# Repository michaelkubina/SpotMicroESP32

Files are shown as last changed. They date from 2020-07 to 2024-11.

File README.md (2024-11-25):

# SpotMicroESP32

My take on a SpotMicro with an optimized design for supportfree 3D-printing and integration of an ESP32-DevKitC. This is still a Work-in-Progress!

You can find the 3D-printing parts on Thingiverse as well: https://www.thingiverse.com/thing:4559827/files

- Join the Discord-Channel for this remix: https://discord.gg/s8F6xHGk9Y (#spotmicro-esp32)
- ~Join the Slack-Channel for this remix - discuss any topics regarding this design: spotmicroai.slack.com (#spotmicro-esp32)~ Due to no active subscription there is no possibility to browse through older posts. This is why a lot of people moved to the discord channel.

This Project currently lacks the whole programming/software part. Luckily Maarten Weyn already made the inverse kinematics work and wrote also an Smartphone App for simple Control of this Robot via BLE. There is no walking gait implementation though. I still advice to take a look into his Repository as well, as this currently my preferred codebase:
https://github.com/maartenweyn/SpotMicro_ESP32

The Discord user Blacksheep created a impressive fork of this project, that utilizes a custom designed PCB for component placement and a FSI6 remote control in order to operate the robot. The codebase implements the inverse kinematics and even walking gait for it. Since its packed as an arduino project, its simpler to get started with it then with the ESP-IDF. You can find the repo here:
https://github.com/Blacksheep909/SpotMicroESP32-Nitro-Fork/tree/master

The SpotMicro-Leika project sources different SpotMicro projects and combines them into a feature-rich build. It offers an FreeRTOS implementation, is under active development and has the inverse kinematics and two gaits implemented. You should definetly check it out:
https://github.com/runeharlyk/SpotMicroESP32-Leika

Also there's a walking gait implementation and voice-commanding by Guna R. from the slacks #spotmicro-esp32 channel, whis is build upon Maartens software (see Repo above). You definitly have to take a look there as well - but it seems the repos sourcecode is incomplete and missing the app:
https://github.com/cholan2100/ceasar

Look also at the GitLab pages for the general SpomicroAI community, where you can find different models and resources: https://gitlab.com/custom_robots/spotmicroai

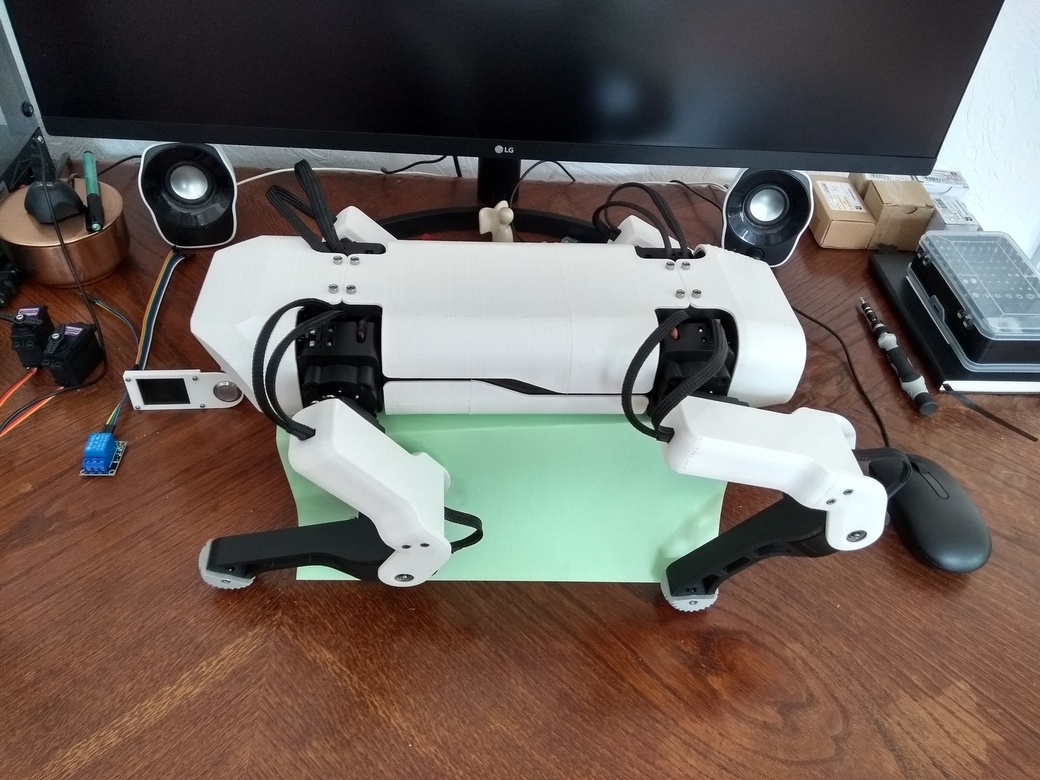
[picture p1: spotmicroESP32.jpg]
SpotMicroESP32


## Note of thanks
I want to thank Deok-yeon Kim (KDY0523) for his beautyful and well thought out design of the SpotMicro, without whom my derivate would not have been possible. You can find his original Design here on Thingiverse: https://www.thingiverse.com/thing:3445283

Him sharing the files with an open licence, made it possible to let it grow a community around it. This is why i want to reference to them as well - the SpotMicroAI Community: https://spotmicroai.readthedocs.io/en/latest/

## Preface
This is a work-in-progress, with rather loose milestones.

For 2020 there are two goals:
- ~to redesign the original parts, so that they could be printed without any support~ (done)
- ~to make a circuitry for all sensors and parts, that possibly would fit and be considered necessary~ (done)

~For 2021 there are two main goals and one optional goal:
- to write my own firmware with the [ESP-IDF](https://github.com/michaelkubina/SpotMicroESP32/tree/master/code#esp-idf), that integrates/utilizes all sensors and modules except the ESP-CAM which needs its own firmware (in progress)
- to write a smartphone App in Flutter, that connects to the firmware and reads from/writes to the robot (in progress)
- to implement the inverse kinematics (optional goal)~

This repository is currently just my hobby and as such, it will have its own pace. This being said, i am still happy about any questions, collaborations, suggestions, ideas, forks and what else comes to your mind. I want you to participate, because i think there are a lot of things, that you could dig into.

## Sections

* [3D-printed Partlist](https://github.com/michaelkubina/SpotMicroESP32/blob/master/parts/SpotMicroESP32_parts_v1_0_0/)
* [Bill of Materials](https://github.com/michaelkubina/SpotMicroESP32/#bill-of-material)
* [Assembly Guide](https://github.com/michaelkubina/SpotMicroESP32/blob/master/assembly/)
* [Electronics](https://github.com/michaelkubina/SpotMicroESP32/blob/master/electronics/)
* [Programming](https://github.com/michaelkubina/SpotMicroESP32/blob/master/code/)
* [Inverse Kinematics](https://github.com/michaelkubina/SpotMicroESP32/blob/master/kinematics/)

## Bill of Material
The following Section will describe in detail the different parts needed for your own SpotMicroESP32 build, with at least some rough estimate of the price.

### 3D-Printing
To build your own SpotMicroESP32 you will need to print a lot parts. For an overview of the 3D printed parts needed, please visit the [3D-printed Partlist](https://github.com/michaelkubina/SpotMicroESP32/blob/master/parts/SpotMicroESP32_parts_v1_0_0/). It might be necessary to remix some of the templates to suit your needs, when chosing other electronic components than those listet here.

### Electronics
The SpotMicroESP32 ist still a Work-in-Progress and as such the BOM might change as well - check the "deprecated" section for changes. There are still some parts missing and some others are not tested yet - those status will be marked as such. I will give a rough price estimate, which may or may not work for you and might be out of date at some point.

| part or module | number | short description | status | estimated price | 
|---|---|---|---|:---|
| ESP32-DevKitC 							|  1x | the core MCU for the build with WIFI + BLE capabilities. 											| tested			| 7€		|
| ESP32-CAM									|  1x | Tested with the ESP32-Module with OV2640 Camera (version 2). There are also cameras with a version 1 OV2640, where the sensor is in landscape orientation and not in portrait. Also the flexcable seems to be some millimeters shorter than the one from Version 2. You can distinguish them by the imprint on the flexcable, stating TY-OV2640-V2.0. Both OV2640 Cameras should work in theory, as the part is designed to fit both models. Definetly dont go with the one with an fisheye-lens or other variations - the field of view would be hindered and most likely the lens would not fit through the hole anyway. 																		| tested	| 10€		|
| FT232RL USB-TTL-Adapter					|  1x | USB-to-Serial Adapter for ESP32-CAM flashing														| tested			| 2€		|
| (MG996R Servo)								| 12x | The bare minimum... but with flaws like jittering and much play... 10Kg servos with metal gears and ball bearings. With these the robot is capable to stand up/change his pose but they are most likely too weak for smooth and reliable walking. **(Update 2020-11-19: It can be affirmed, that walking is possible not great, but also not horrible)** Go with these only if you can accept these limitations and if more expensive servos would mean not to try this project in the first place.  										| tested			| 5€ each 	|
| better go with DS3218MG Servo 			| up to 12x | 20Kg servos with metal gears and ball bearings. Much less play and in my tests no jittering, but also very strong. With these your robot should be able to walk **significantly better**. Maybe only 4 of these are enough, when used in the lower legs - the most stressed parts. Maybe you would need also 4 additional ones for the upper legs - but maybe MG996R are enough here. The shoulders should be comfortable with MG996R, as these dont do much heavy work.  														| partially tested	| 15€-20€ each 	|
| FSH6S Servohorn 							| 12x | servohorn used for this build (should be already shipped with your servos) otherwie use model from 3D parts 							| tested 			| n.n. 		|
| Rubber Dampeners for your Servos			| 48x | servo rubber dampeners, so you could use M3 screws (should be already shipped with your servos) 	| tested 			| n.n. 		|
| Servocable Extension						|  4x | extending the servocables of the lower legs about 10cm to 15cm 										| tested			| 10€		|
| 625ZZ Ball Bearing 						|  8x | miniature ball bearing without a flange 															| tested 			| 1€ each 	|
| WS2812b 12 LED Ring (50mm outer diameter) |  1x | Neopixel-Clone-Ring with an outer diameter of 50mm used to signal status/mood						| tested | 6€ |
| 0.96" OLED I2C Display					|  1x | small OLED screen with SSD1306 IC for status informations											| tested			| 4€		|
| HC-SR04 Ultrasonic Sensor					|  2x | ultrasonic sensor module for distance measuring														| tested			| 3€ each	|
| GY-521 Gyroscope and Accelerometer		|  1x | a module to measure accelaration and spatial orientation, which can be extented with magnetometers  | tested			| 3€		|
| PCA9685 16Channel 12Bit PWM Board			|  1x | PWM driver board used for your servos and LEDs, which can power your parts from an external source	| tested			| 5€		|
| HW-482 / KY-019 5V 10A Relais				|  1x | relais module to cut the power to your servos completely											| tested			| 3€		|
| 19mm Push Button with LED					|  1x | illuminated latching pushbutton 																	| tested			| 10€		|
| Micro-USB to DIP Adapter					|  2x | USB-Ports used for extending the USB-Ports of the ESP32 DevKitC and ESP32-CAM (TTL-Adapter)			| tested			| 2€		|
| XL4016 DC-DC 9A Stepdown Converter  		|  1x | big step-down converter to lower your LiPo 2S voltage to 6,5V **(minimum for MG996R)** | tested		 | 8€		|
| or SZBK07 DC-DC 20A Stepdown Converter  	|  1x | even bigger step-down converter to lower your LiPo 2S voltage to 6,5V **(minimum for DS3218)**	| tested		 | 12€		|
| LM2596 DC-DC or similar Stepdown Module	|  1x | small step-down converter to lower your LiPo 2S voltage 5V for ESP32's VIN and Modules 				| tested			| 2€ each	|
| ACS712 30A current sensor module			|  1x | current sensor module capable of max. 30A for e.g. emergency shutdown				 				| tested			| 2€ 		|
| 25V voltage sensor module					|  1x | simple voltage divider module for up to 25V used as a voltage sensor to determin battery charge		| tested			| 2€ 		|
| 5200mAh - 6200mAh LiPo 30C+ 2S Tamiya/XH	|  1x | beefy LiPo as your main power source ***(this is actually your individual choice)***				| tested		 	| 40€		|

#### Depecrated

The Camera-Unit in the head will be replaced by an ESP32-CAM, because its reasonably cheap (~10€) and opens up a lot of new possibilities like object-recognition, because of additional processing-power.

| part or module | number | short description | status | estimated price | 
|---|---|---|---|:---|
| OV7670 VGA-Camera Module w/o FIFO			|  1x | VGA-Camera without framebuffer IC, used with lower resolution due to memory restrictions **(replaced by ESP32-CAM)**			| tested			| 3€		|
| 5mm ~3V LEDs (White)						|  6x | LEDs used as your camera-lights	**(replaced by ESP32-CAM internal flashlight)**													| tested			| 1€		|
| 5mm ~3V RGB-LEDs							|  2x | RGB-LEDs used as an underglow, might signal status or mood **(replaced by Neopixel-Generica)**									| tested			| 1€		|
| 1,77" TFT with ST7735 w/o SD				|  1x | small TFT screen with ST7735 IC for status informations **(replaced by 1.8" TFT with SD-Card)**									| tested			| 7€		|
| optional WS2812B Pixelboard				|  4x | Neopixel-Clones (SMD LED's on small round PCB) used as an underglow, might signal status or mood	**(removed, as the result is underwealming** | tested			| 1€		|
| 1,8" TFT with ST7735 with SD				|  1x | small TFT screen with ST7735 IC for status informations	**(replaced by 0.96" OLED I2C Display)**	 |tested			| 7€		|

### Miscellaneous

| part or module | number | short description | status | estimated price | 
|---|---|---|---|:---|
| M2x8 cylinderhead screws + M2 nuts		| 84x each | screws + nuts to mount your servohorns ***(you could glue the servohorns in place instead and save yourself 72x M2x8 screws and nuts, but i have not tested it)***, also used to mount the 1,77" TFT and the pins for the ball bearings 	| tested | 8€  |
| M3x8 cylinderhead screws + M3 nuts		| 80x each | screws + nuts for the whole assembly ***(i hope i have not forgotten some, better buy in bulk as these are usefull for other projects as well)***																							| tested | 8€  |
| M3x20 cylinderhead screws + M3 nuts		| 64x each | screws + nuts to mount your servos and assemble the upper legs																																												| tested | 12€ |
| lots of cables and connectors and stuff	| | it's up to you which cables or wires and connectors you want to use, or if you would like to solder everything into place, and if you use heat shrinks, fabric hoses 																		| up to you | 20€ |
| PLA + TPU (***?***)						| | you will need about 1Kg of PLA + some grams of TPU (eg. my Black/White design: 500g for the covers + upper legs, 500g for the chassis + lower legs + shoulder joints, some small grams for the grey sensorplate in the head) + some grams of TPU for the foottips | tested | 30€+ |

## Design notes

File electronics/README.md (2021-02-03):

# Electronics #

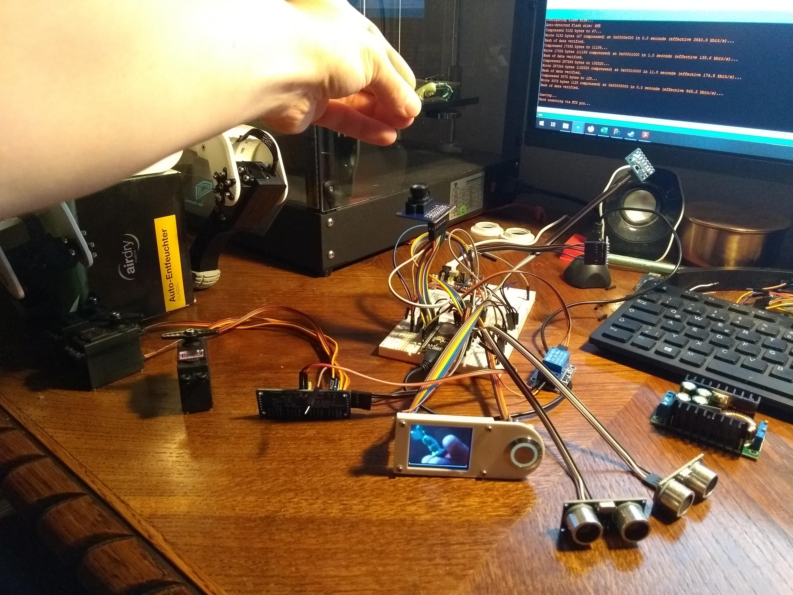
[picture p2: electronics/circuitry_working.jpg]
Circuitry Milestone


## Resources ##

You can find an excel-sheet in this sections, which describes the basic pin-assignments. You can find older documents in the archives subfolder.

## Wiring ##

When wiring your own robot, think of some kind of color coding for your wires, so its easier to distuingish them - for example:
* 5V with violett wires
* 3.3V with red wires
* I2C Clock white
* I2C Data grey
* Analog Signals ocker 
* etc...

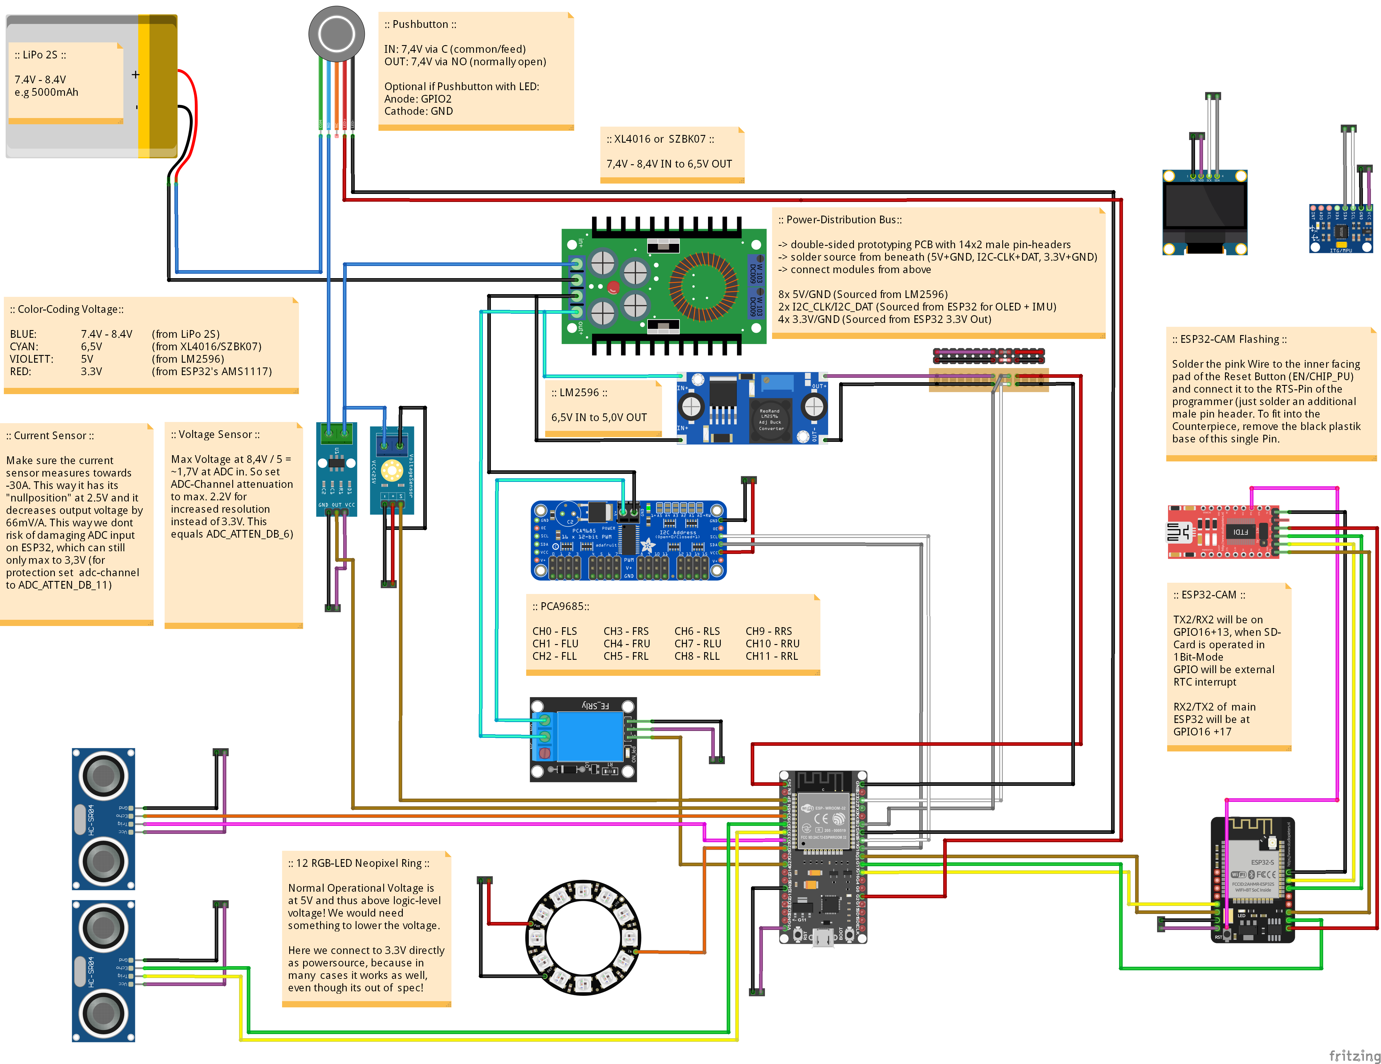
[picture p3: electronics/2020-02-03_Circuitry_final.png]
Fritzing Diagram


## Images ##

Some images from my build, but not the latest - update in development.

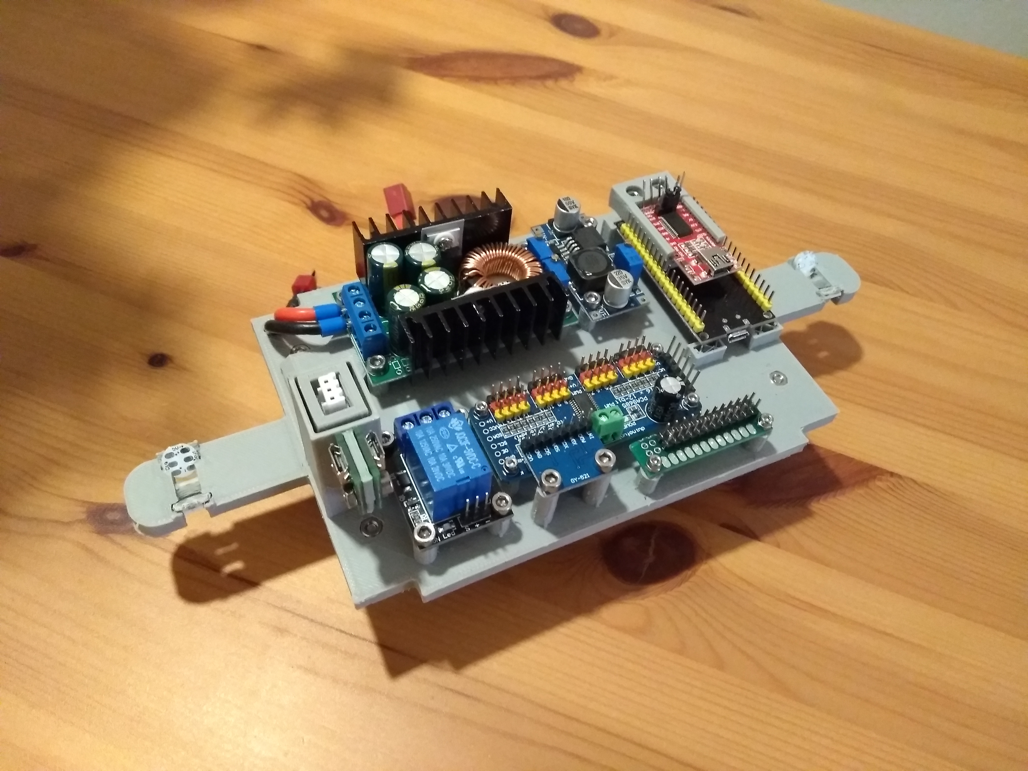
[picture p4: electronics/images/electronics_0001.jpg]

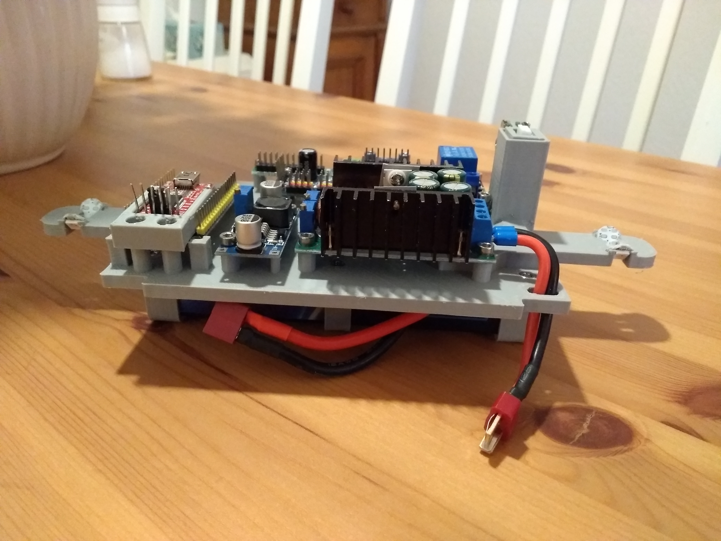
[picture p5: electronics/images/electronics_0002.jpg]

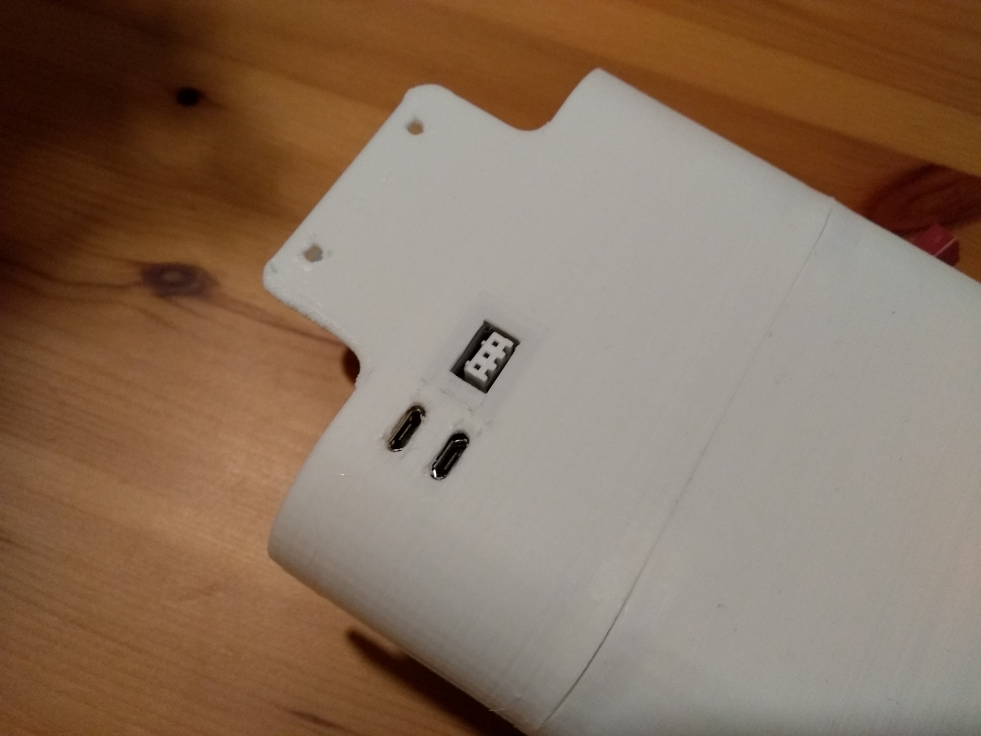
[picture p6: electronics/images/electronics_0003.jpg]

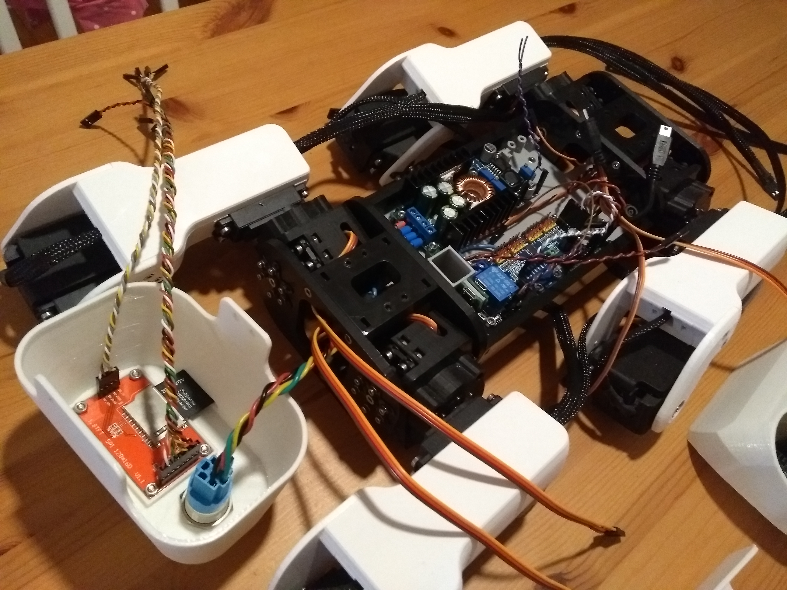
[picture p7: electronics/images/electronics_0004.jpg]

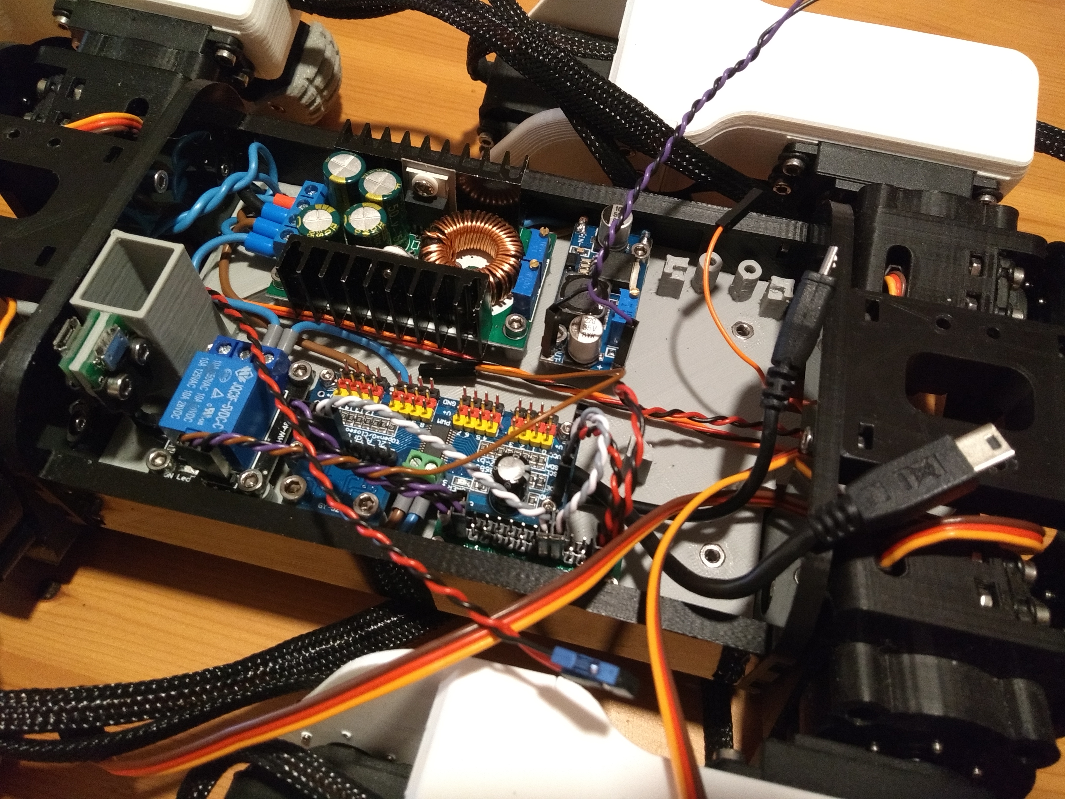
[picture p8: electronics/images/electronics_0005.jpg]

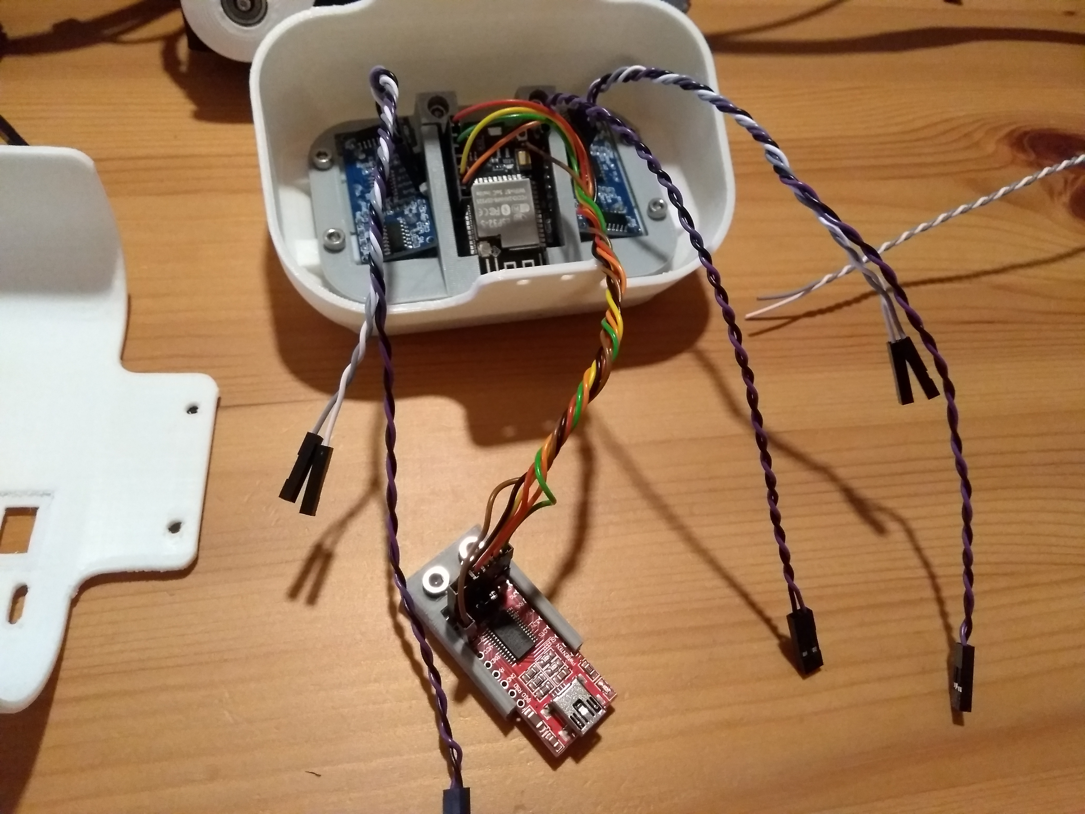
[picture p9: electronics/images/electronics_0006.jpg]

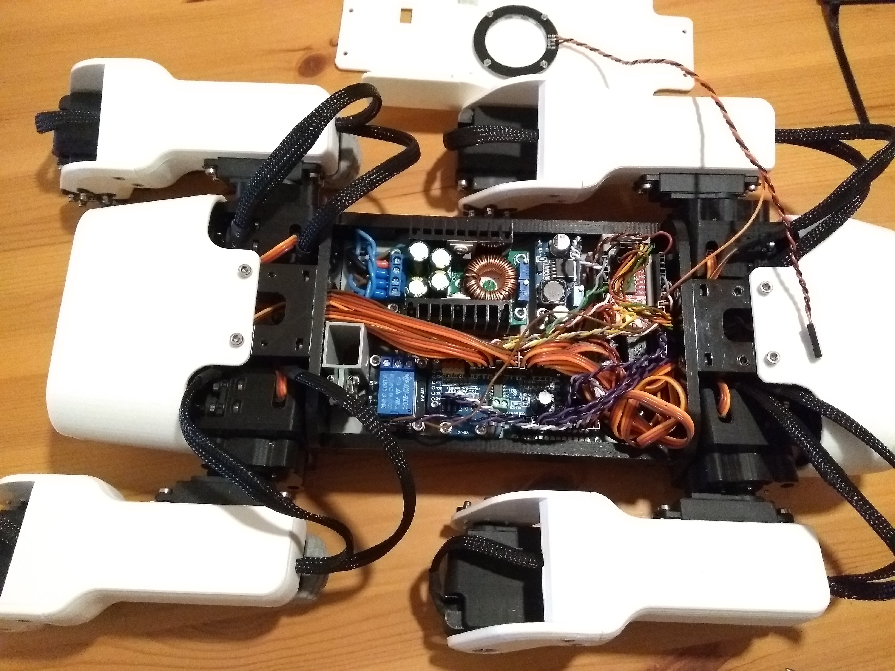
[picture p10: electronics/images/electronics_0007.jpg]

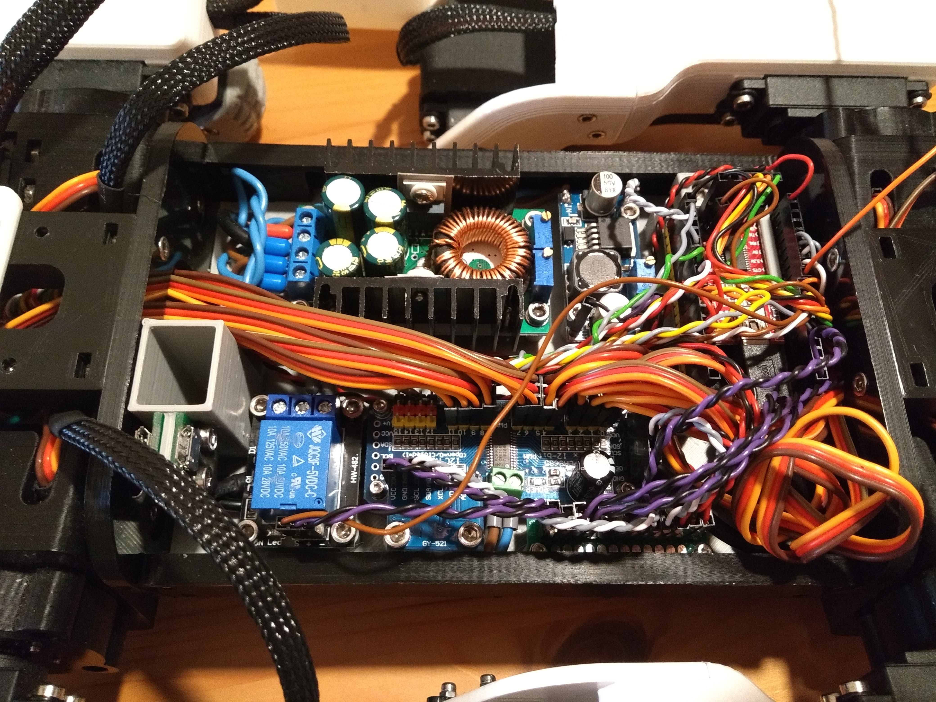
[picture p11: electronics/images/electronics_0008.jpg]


### SERVO DRIVER - PCA9685 ###

Manufacturer Homepage: https://www.nxp.com/products/power-management/lighting-driver-and-controller-ics/ic-led-controllers/16-channel-12-bit-pwm-fm-plus-ic-bus-led-controller:PCA9685
Datasheet: https://www.nxp.com/docs/en/data-sheet/PCA9685.pdf

The PCA9685 is capable of FastMode+ (I2C clock at 1Mhz) - it should have its own I2C bus - which gives us more update cycles on the servos. The MG996R even though most tutorials and sellers claim their working frequency to be 50Hz, we can actually go to even 333Hz and beyond. The limit is only the 12Bit resolution and the maximum value for your servo for the max-angle. The pulsewidth of about 2ms + about 0.3ms is whats relevant for the IC in these digital servos.

Do not use Standard Mode - 100KHz
Do not use FastMode - 400KHz
Go with FastMode+ - 1MHz

| Channel | Servo | Abbreviation |
|---|---|---|
| CH0 | Front Left Shoulder | FLS |
| CH1 | Front Left Upper Leg  | FLU |
| CH2 | Front Left Lower Leg  | FLL |
| CH3 | Front Right Shoulder  | FRS |
| CH4 | Front Right Upper Leg | FRU |
| CH5 | Front Right Lower Leg | FRL |
| CH6 | Rear Left Shoulder | RLS |
| CH7 | Rear Left Upper Leg | RLU |
| CH8 | Rear Left Lower Leg | RLL |
| CH9 | Rear Right Shoulder | RRS |
| CH10 | Rear Right Upper Leg  | RRU |
| CH11 | Rear Right Lower Leg  | RRL |
| CH12 | x | x |
| CH13 | x | x |
| CH14 | x | x |
| CH15 | x | x |

### CURRENT SENSOR - ACS712 30A ###

Manufacturer Homepage: https://www.allegromicro.com/en/products/sense/current-sensor-ics/zero-to-fifty-amp-integrated-conductor-sensor-ics/acs712
Datasheet: https://www.allegromicro.com/~/media/files/datasheets/acs712-datasheet.ashx

### 0,96" OLED - SSD1306 ###

Manufacturer Homepage: https://www.solomon-systech.com/en/product/advanced-display/oled-display-driver-ic/ssd1306/
Datasheet: https://cdn-shop.adafruit.com/datasheets/SSD1306.pdf

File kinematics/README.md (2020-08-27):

# Inverse Kinematics #

**still a lot to do**

## The legs ##

The length-measurements of the legs is performed on the centers of the rotational axis and from the perspective of the foottip touching the ground in its center.

* L1: 10mm
* L2: 60,5mm
* L3: 111,1mm (resp. L3a: 107mm / L3b: 30mm)
* L4: 118,5mm

The foot-tip actually just elevates the body 20mm from the ground on every leg and is because of this disregarded for now.

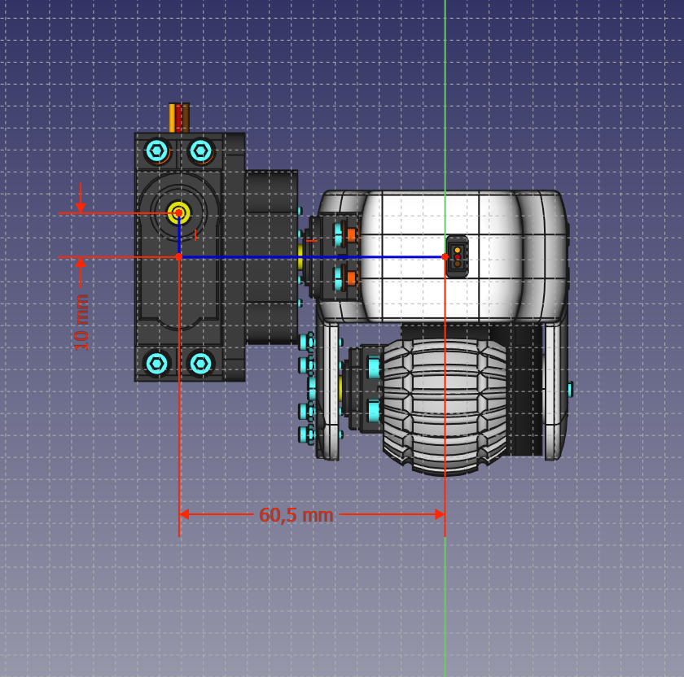
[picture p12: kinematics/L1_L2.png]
L1_L2


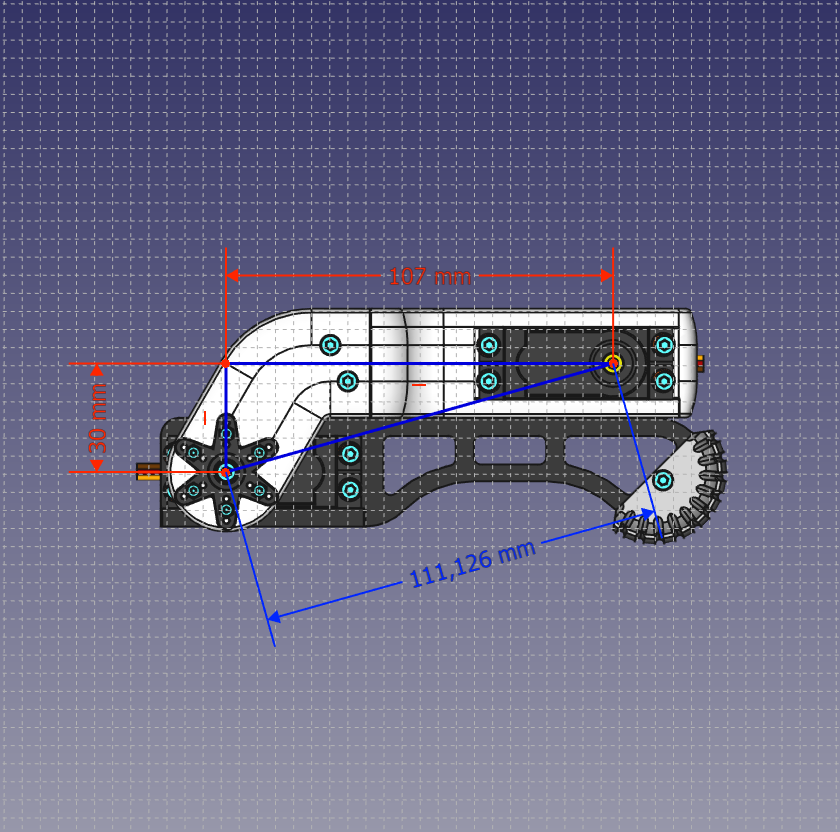
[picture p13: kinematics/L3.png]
L3


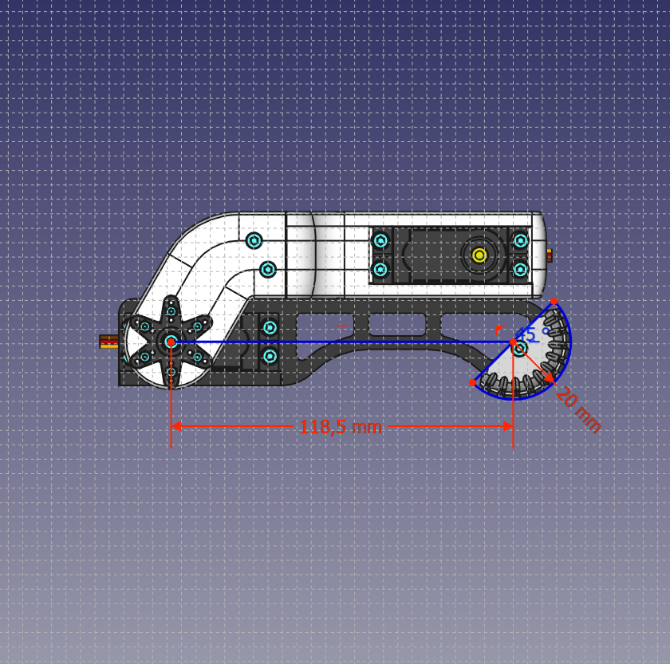
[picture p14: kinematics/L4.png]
L4


## The body ##
The body (the plane where the four legs are attached to) is 78mm \* 207,5mm. The axis of the front and rear leg-pairs are 78mm apart, while the center of the first rotational axis of the legs is 207,5mm apart. The 207,5mm are the sum of the chassis side (150mm), both inner shoulders (each 5mm thick) and two times the halfes of the bottom/top shoulder blocks (2 \* 23,75mm = 47,5mm).

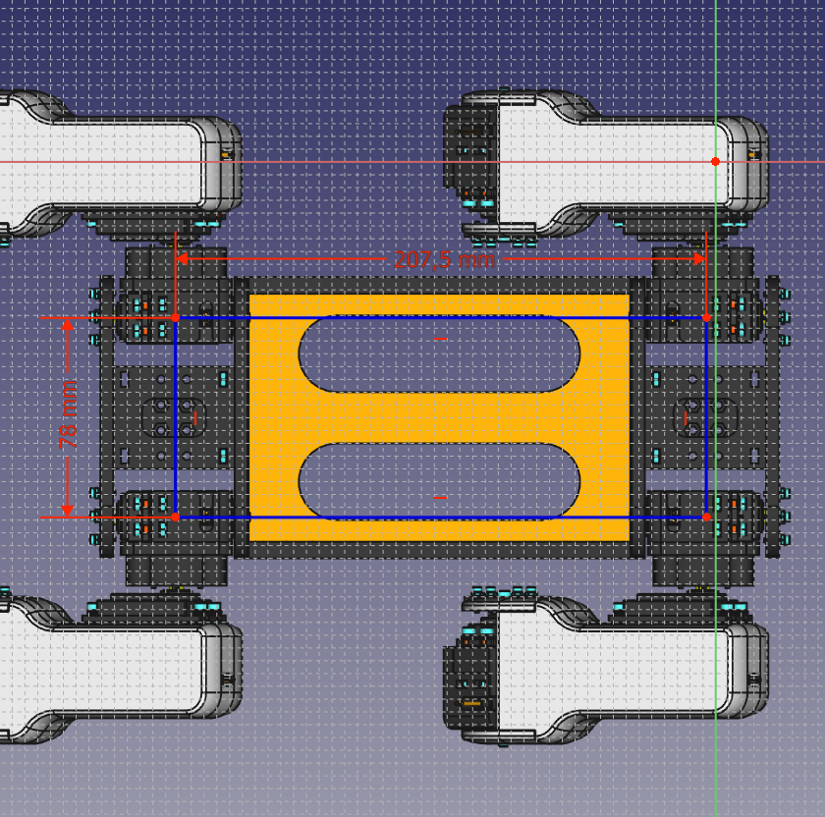
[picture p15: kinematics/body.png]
Body


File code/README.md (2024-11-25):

# Programming #

## Firmware and Control by Blacksheep909 ##

The Discord user Blacksheep created a impressive fork of this project, that utilizes a custom designed PCB for component placement and a FSI6 remote control in order to operate the robot. The codebase implements the inverse kinematics and even walking gait for it. Since its packed as an arduino project, its simpler to get started with it then with the ESP-IDF. You can find the repo here:
https://github.com/Blacksheep909/SpotMicroESP32-Nitro-Fork/tree/master

## Firmware and Build by runeharlyk ##

The SpotMicro-Leika project sources different SpotMicro projects and combines them into a feature-rich build. It offers an FreeRTOS implementation, is under active development and has the inverse kinematics and two gaits implemented. You should definetly check it out:
https://github.com/runeharlyk/SpotMicroESP32-Leika

## Firmware and App by Maarten Weyn ##

This Project currently lacks the whole programming/software part. Luckily Maarten Weyn already made the inverse kinematics work and wrote also an Smartphone App for simple Control of this Robot via BLE. Take a look into his Repository as well:
https://github.com/maartenweyn/SpotMicro_ESP32

### Quickstart Maartens Firmware ###

* calibrate your servos (do this before assembly, otherwise you have more work to do). You can find here a [quick explanation of how to achieve this](https://github.com/michaelkubina/SpotMicroESP32/tree/master/assembly#servo-calibration).
* install the [ESP-IDF in VSCode](https://github.com/michaelkubina/SpotMicroESP32/tree/master/code#esp-idf) for the firmware-developement and get [Cordova](https://github.com/maartenweyn/SpotMicro_ESP32/tree/master/code/cordova) for the app-developement running
* clone [maartens firmware-repo](https://github.com/maartenweyn/SpotMicro_ESP32/tree/master/code/esp-idf/ik_test) and 
	* account for the missing relay in his code. You can overcome the relay being in the way in two ways:
		* connect NC instead of NO (always active after power-up, if no signal to the relay) to your PCA9685 V+ (terminal block) and switch it back, once you have a solid code-base that accounts for it.
		* OR do the code-thing right away and leave it as it is...like this:
			**config.h**
			```
			#define RELAY_IO    27
			```

			**main.c -> void app_main()**
			
			```
			...
			gpio_pad_select_gpio(RELAY_IO);
			gpio_set_direction(RELAY_IO, GPIO_MODE_OUTPUT);
			gpio_set_level(RELAY_IO,1); // 1 = on, 0 = off
			```
	* clone the [esp-dsp (digital signal processing)](https://github.com/espressif/esp-dsp) **component** into maartens repo's corresponding component folder
	* compile and flash
* compile the cordova app and flash onto your android phone (or iphone, but i dont own an iphone and cant help here)
* install [arduino ide](https://randomnerdtutorials.com/installing-the-esp32-board-in-arduino-ide-windows-instructions/)
	* get this [firmware for your ESP32-CAM](https://github.com/easytarget/esp32-cam-webserver)
	* add your local wifi credentials to the configuration
	* flash the ESP32_CAM with this firmware and access the live-stream/cam interface via your webbrowser

## Firmware by Guna ##

An walking gait implementation and voice-commanding was achieved by Guna R. from the slacks #spotmicro-esp32 channel, whis is build upon Maartens software (see Repo above). You definitly have to take a look there as well and contribute:
https://github.com/cholan2100/ceasar

**Work-in-Progress : still a lot to do**

This section currently contains some basic test-programs for servo-calibration and circuit-/module-tests. 

## Arduino IDE ##

You can use the Arduino IDE for the developement of your ESP32 programs. A good resource for the setup can be found here:

[Setup Arduino IDE](https://randomnerdtutorials.com/installing-the-esp32-board-in-arduino-ide-windows-instructions/)

## ESP-IDF ##

The ESP-IDF is the developement framework provided by Espressif. Here's the official documentation how to get started:

[Setup ESP-IDF](https://docs.espressif.com/projects/esp-idf/en/latest/esp32/get-started/index.html#get-started)

### Quick Installation Guide - Downloads ###

If you don't want to get into the hurdle to install the ESP-IDF via the official documentation, you can follow this quick installation guide. It has been only tested for Windows 10 machines, so the Steps on Linux or Mac OS X will vary.

For a complete Installation you will need to install:

* [Python](https://www.python.org/downloads/)
* [Git](https://git-scm.com/download/win)
* [MinGW-w64](http://mingw-w64.org/doku.php/download/mingw-builds)
* [Visual Studio Code (VSCode)](https://code.visualstudio.com/download)
* [C/C++ Extension for VSCode](https://marketplace.visualstudio.com/items?itemName=ms-vscode.cpptools)
* [ESP-IDF Extension for VSCode (from VSCode Marketplace)](https://marketplace.visualstudio.com/items?itemName=espressif.esp-idf-extension)

### Quick Installation Guide - Steps ###

1. Install Python by checking the "Add Python _VERSION_ to PATH" checkbox and simply choose the "Install Now" option. If you are interested in a more detailed description how to further setup Python, it can be found here: [Official Python Install Guide](https://docs.python.org/3/using/windows.html)
1. Install Git
1. Install MinGW-w64 and choose a simpler installation directory path like C:\MinGW\
1. Install VSCode - if you are interested in some more informations about the VSCode Setup than take a look at the [Official VSCode Setup Documentation](https://code.visualstudio.com/docs/setup/setup-overview)
1. Start VSCode and 
	1. install the C/C++ Extension from the VSCode Marketplace
	1. install the ESP-IDF Extension from the VSCode Marketplace. Use the Express Install as mentioned here: [VSCode ESP-IDF Extension Github](https://github.com/espressif/vscode-esp-idf-extension/blob/master/docs/SETUP.md#setup-wizard)
		1. update some of your *system variables*
			1. add ";%IDF_PATH%\tools" to PATH
			1. add a new variable named "IDF_PATH" with the value "C:\Users\INSERT_YOUR_USER_DIRECTORY\esp\esp-idf"
	1. add the path to the MinGW C-Standard Libraries Headers to your C/C++ configuration in VSCode
		1. Press F1 for the Command Menu
		1. type and choose "C/C++: Edit Configuration (UI)" and navigate to the "advanced settings" at the bottom
		1. add your path (example below) to the browse.path:  
			${config:idf.espIdfPath}/components  
			${config:idf.espIdfPathWin}/components  
			${workspaceFolder}  
			*C:\MinGW\mingw64\x86_64-w64-mingw32\include*
1. Done!

### Starting a new Project ###

Either open a available project/firmware (like the one from Maarten Weyn or Guna) in VSCode or start your own via:

1. Add a folder to your Workspace "Edit -> Add Folder to Workspace"
1. Press F1 for the Command Menu and type "ESP-IDF: Create Project" - a more detailed description can be found here: [Official VSCode-ESP-IDF-Extension How-to-Use](https://github.com/espressif/vscode-esp-idf-extension#how-to-use)
	1. Choose the App-Template
	1. Change "project" within the CMakeLists.txt to whatever you want to call yours
1. Have fun coding!

Everything you need to know, can be found in the [Official ESP-IDF API Reference](https://docs.espressif.com/projects/esp-idf/en/latest/esp32/api-reference/index.html)	alongside with many linked example-projects to their [Github Examples Page](https://github.com/espressif/esp-idf/tree/master/examples).

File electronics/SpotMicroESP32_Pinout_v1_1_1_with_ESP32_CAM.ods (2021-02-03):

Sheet: ESP32 DevKitC Connections
TO POWERBUS 3V3 |  |  | 3.3V | GND | TO POWERBUS 3V3
 |  |  | EN | GPIO 23
 | Signal | VOLTAGE SENSOR | GPIO 36 | GPIO 22 | I2C | Clock | TO POWERBUS I2C CLK
 | OUT | CURRENT SENSOR | GPIO 39 | GPIO 1
 | ECHO | right HC-SR04 | GPIO 34 | GPIO 3
 | ECHO | left HC-SR04 | GPIO 35 | GPIO 21 |  | Data | TO POWERBUS I2C DATA
 | TRIG | left HC-SR04 | GPIO 32 | GND | PUSHBUTTON | LED GND
 | TRIG | right HC-SR04 | GPIO 33 | GPIO 19 | PCA9685 | I2C Clock
 | DATA | NEOPIXEL Ring | GPIO 25 | GPIO 18 |  | I2C Data
 |  |  | GPIO 26 | GPIO 5 | ESP-CAM | EXT-INT
 | SIGNAL | RELAY | GPIO 27 | GPIO 17 |  | RX
 |  |  | GPIO 14 | GPIO 16 |  | TX
 |  |  | GPIO 12 | GPIO 4
FROM POWERBUS 5V |  |  | GND | GPIO 0
 |  |  | GPIO 13 | GPIO 2 | PUSHBUTTON | LED
 |  |  | GPIO 9 | GPIO 15
 |  |  | GPIO 10 | GPIO 8
 |  |  | GPIO 11 | GPIO 7
FROM POWERBUS 5V |  |  | 5V | GPIO 6

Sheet: ESP32-CAM
 | SD_DATA 1 | FLASHLIGHT | GPIO4 | GND
SD-CARD 1Bit Mode (SPI-MODE) | SD_DATA 0 |  | GPIO2 | TX | FTDI | RX
 | SD_CLK |  | GPIO14 | RX | FTDI | TX
 | SD_CMD |  | GPIO15 | 3V3 / 5V OUT
 | SD_DATA3 | RX | GPIO13 | GND | FTDI | GND
 | SD_DATA2 | RTC Interrupt | GPIO12 | GPIO0 | FTDI | DTR
FROM POWERBUS 5V |  |  | GND | GPIO16 | TX
FROM POWERBUS 5V |  |  | 5V | 3V3 | FTDI | VCC
 |  |  |  | EN | FDTI | RTS | Solder Cable to Reset-Button (the end facing inwards)

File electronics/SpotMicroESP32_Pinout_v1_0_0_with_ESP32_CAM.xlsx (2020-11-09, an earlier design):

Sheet: ESP32 DevKitC Connections
POWERBUS 3V3 |  |  | 3.3V | GND | POWERBUS 3V3
 |  |  | EN | GPIO 23 | TFT | SDA | SPI Data
 |  |  | GPIO 36 | GPIO 22 | I2C | Clock | POWERBUS I2C CLK
 |  |  | GPIO 39 | GPIO 1
 | ECHO | right HC-SR04 | GPIO 34 | GPIO 3
 | ECHO | left HC-SR04 | GPIO 35 | GPIO 21 |  | Data | POWERBUS I2C DATA
 | TRIG | left HC-SR04 | GPIO 32 | GND | PUSHBUTTON | LED GND
 | TRIG | right HC-SR04 | GPIO 33 | GPIO 19 | TFT | A0 | Data Command
 | DATA | NEOPIXEL Ring | GPIO 25 | GPIO 18 |  | SCK | SPI Clock
 | DATA | NEOPIXEL Underglow | GPIO 26 | GPIO 5 |  | CS | Chip Select
 | SIGNAL | RELAY | GPIO 27 | GPIO 17 | ESP32-CAM | RX
 | SD_SCK | SD | GPIO 14 | GPIO 16 |  | TX
 | SD_MISO |  | GPIO 12 | GPIO 4 | TFT | RESET | Reset
POWERBUS 5V |  |  | GND | GPIO 0 |  | LED | LED Backlight
 | SD_MOSI | SD | GPIO 13 | GPIO 2 | PUSHBUTTON | LED
 |  |  | GPIO 9 | GPIO 15 | SD | SD_CS
 |  |  | GPIO 10 | GPIO 8
 |  |  | GPIO 11 | GPIO 7
POWERBUS 5V |  |  | 5V | GPIO 6

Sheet: ESP32-CAM
 | SD_DATA 1 | FLASHLIGHT | GPIO4 | GND
SD-CARD 1Bit Mode (SPI-MODE) | SD_DATA 0 |  | GPIO2 | TX | FTDI | RX
 | SD_CLK |  | GPIO14 | RX | FTDI | TX
 | SD_CMD |  | GPIO15 | 3V3 / 5V OUT
 | SD_DATA3 | RX | GPIO13 | GND | FTDI | GND
 | SD_DATA2 | TX | GPIO12 | GPIO0 | FTDI | DTR
 | POWERBUS |  | GND | GPIO16
 | POWERBUS |  | 5V | 3V3 | FTDI | VCC
 |  |  |  | EN | FDTI | RTS | Solder Cable to Reset-Button (the end facing inwards)

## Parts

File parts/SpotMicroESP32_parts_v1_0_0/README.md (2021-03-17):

# Parts
This section gices an overview of all necessary parts and their compatibility to the original KDY0523-Spotmicro. For the assembly please read the [Assembly Guide](https://github.com/michaelkubina/SpotMicroESP32/blob/master/assembly/). You will need at least the screws and nuts from the [Bill of Materials](https://github.com/michaelkubina/SpotMicroESP32/#bill-of-material).

## Mods
There are some modifications available (e.g. moulds for silicone feet or modifications to use metaldisc servohorns). Take a look into the mods folder, if there is anything of interest or if you have your own modifications, than state a pull request:

[MODS-Section](https://github.com/michaelkubina/SpotMicroESP32/blob/master/parts/SpotMicroESP32_parts_v1_0_0/mods/)  

## Partlist
The SpotMicroESP32 uses parts, that where redesign from the ground. These are largely incompatible to the original KDY0523-Spotmicro - meaning they are as an assembly not interchangable. This is due to some design decisions, that include the ability to print without support, using less different screw sizes and repositioning screwholes or altering dimensions to achive a more convenient and fluid design. The following list will not only provide informations about the total amount of prints needed (including the amount of mirrored copies), but if its compatible with the original KDY0523-Spotmicro and how many mirrored copies you would need of it.

### Chassis
This assembly is **not compatible** with the KDY0523-Spotmicro

| Thumbnail | Name | normal copies | mirrored copies | total amount | infill | total weight |
|---|---|---|---|---|---|---|
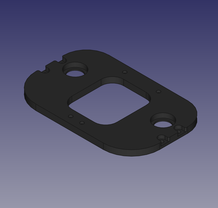
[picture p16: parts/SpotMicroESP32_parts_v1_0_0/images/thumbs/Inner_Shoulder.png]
Inner Shoulder Thumbnail
| 									| Inner Shoulder					| 2 | - | 2 |  20% |  32g |
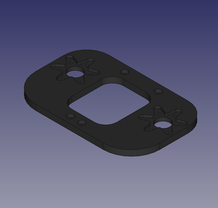
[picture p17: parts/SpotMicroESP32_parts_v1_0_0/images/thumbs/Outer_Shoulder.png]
Outer Shoulder Thumbnail
| 									| Outer Shoulder					| 2 | - | 2 |  20% |  32g |
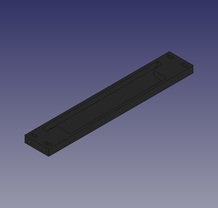
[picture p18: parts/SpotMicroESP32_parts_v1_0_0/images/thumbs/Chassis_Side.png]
Chassis Side Thumbnail
| 										| Chassis Side						| 2 | - | 2 |  20% |  22g |
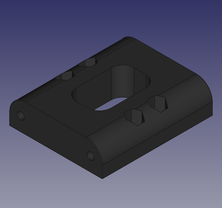
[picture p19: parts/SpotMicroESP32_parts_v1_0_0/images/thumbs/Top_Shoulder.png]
Top Shoulder Thumbnail
| 										| Top Shoulder						| 2 | - | 2 |  20% |  20g |
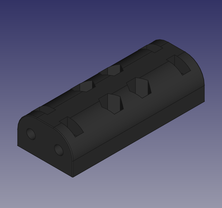
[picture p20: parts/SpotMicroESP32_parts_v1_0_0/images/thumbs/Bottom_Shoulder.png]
Bottom Shoulder Thumbnail
| 									| Bottom Shoulder					| 2 | - | 2 |  20% |  12g |
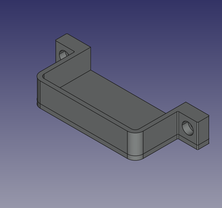
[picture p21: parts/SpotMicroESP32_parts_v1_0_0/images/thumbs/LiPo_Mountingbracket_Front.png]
LiPo Mountingbracket Front Thumbnail
| 			| LiPo Mountingbracket Front		| 1 | - | 1 |  20% | 5g |
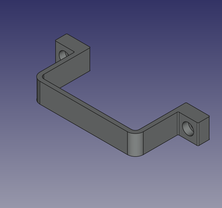
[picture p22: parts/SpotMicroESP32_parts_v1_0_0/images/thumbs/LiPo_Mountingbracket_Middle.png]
LiPo Mountingbracket Middle Thumbnail
| 			| LiPo Mountingbracket Middle		| 1 | - | 1 |  20% | 3g |
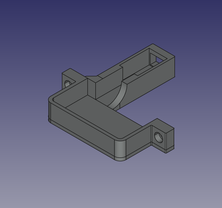
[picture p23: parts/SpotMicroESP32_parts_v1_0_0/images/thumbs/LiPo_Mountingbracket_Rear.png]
LiPo Mountingbracket Rear Thumbnail
| 				| LiPo Mountingbracket Rear			| 1 | - | 1 |  20% | 7g |
| Circuitry Mountingplate Thumbnail					| Circuitry Mountingplate for XL4016			| 1 | - | 1 |  20% |  56g |
| Circuitry Mountingplate Extended Thumbnail					| Circuitry Mountingplate for XL4016 with Extensions			| 1 | - | 1 |  20% |  66g |
| Circuitry Mountingplate Thumbnail					| Circuitry Mountingplate for SZBK07			| 1 | - | 1 |  20% |  56g |
| Circuitry Mountingplate Extended Thumbnail					| Circuitry Mountingplate for SZBK07 with Extensions			| 1 | - | 1 |  20% |  66g |
| TTL Counterpiece Thumbnail								| TTL Counterpiece 					| 1 | - | 1 |  20% | 5g |
| Circuitry Mountingplate Template Thumbnail		| Actual Circuitry Mountingplate Template		| - | - | - | - | - |
| Circuitboard Mount Template Thumbnail		| Simple Mountingplate Template		| - | - | - | - | - |

### Shoulder Joints 
This assembly is compatible with the KDY0523-Spotmicro

| Thumbnail | Name | normal copies | mirrored copies | total amount | infill | total weight |
|---|---|---|---|---|---|---|
| Shoulder Joint Servomount Thumbnail				| Shoulder Joint Servomount			| 2 | 2 | 4 |  20% |  48g |
| Shoulder Joint Servohorn Cap Thumbnail		| Shoulder Joint Servohorn Cap		| 4 | - | 4 |  20% |  28g |
| Shoulder Joint Ball Bearing Pin Thumbnail	| Shoulder Joint Ball Bearing Pin	| 4 | - | 4 |  20% | 4g |

### Leg
This assembly is compatible with the KDY0523-Spotmicro

**Important note**
You should use the "long version", which will result in the legs being fully bend when the robot is in its resting position. The upper and lower leg will be parallel in the end.
The "normal version" copies the dimensions of the original design, which results in the legs not being able to fully collapse. This means the legs will always look like an angle bracket in the end. Maybe with some force you could damage some parts as well, because theoretically you would be able to "overbend" the joint.

| Thumbnail | Name | normal copies | mirrored copies | total amount | infill | total weight |
|---|---|---|---|---|---|---|
| Limb Top Shell Thumbnail									| Limb Top Shell					| 2 | 2 | 4 |  20% |  92g |
| Limb Bottom Shell Thumbnail								| Limb Bottom Shell Thumbnail		| 2 | 2 | 4 |  20% | 100g |
| Limb Ball Bearing Mount Thumbnail			| Limb Ball Bearing Mount **long**	| 2 | 2 | 4 |  20% |  20g |
| Limb Servohorn Mount Thumbnail				| Limb Servohorn Mount **long**		| 2 | 2 | 4 |  20% |  20g |
| Wrist Thumbnail														| Wrist							| 2 | 2 | 4 |  20% | 104g |
| Wrist Counterpart Thumbnail							| Wrist Counterpiece					| 2 | 2 | 4 |  20% |  36g |
| Shoulder Joint Ball Bearing Pin Thumbnail	| Shoulder Joint Ball Bearing Pin	| 4 | - | 4 |  20% | 4g |
| Foot Tip Thumbnail												| Foot Tip							| 4 | - | 4 |  20% |  24g |

### Hull
This assembly is **not compatible** with the KDY0523-Spotmicro

| Thumbnail | Name | normal copies | mirrored copies | total amount | infill | total weight |
|---|---|---|---|---|---|---|
| Front Cover Optimized Thumbnail						| Front Cover Optimized				| 1 | - | 1 | 100% |  58g |
| Sensormount ESP32-CAM Thumbnail											| Sensormount for the ESP32-CAM						| 1 | - | 1 |  20% |  17g |
| Cameramount ESP32-CAM Thumbnail											| Cameramount for the ESP32-CAM	 					| 1 | - | 1 |  20% |  15g |
| Cameramount ESP32-CAM Counterpiece Thumbnail											| Cameramount Counterpiece for the ESP32-CAM	 					| 1 | - | 1 |  20% |  4g |
| Sensormount Thumbnail											| Sensormount **(deprecated)**						| 1 | - | 1 |  20% |  17g |
| Cameramount Thumbnail											| Cameramount **(deprecated)**	 					| 1 | - | 1 |  20% |  15g |
| Rear Cover Shell Long Thumbnail						| Rear Cover Shell Longer Version					| 1 | - | 1 | 100% |  40g |
| Rear Cover Plate Thumbnail								| Rear Cover Plate									| 1 | - | 1 | 100% |  20g |
| Rear Cover Plate Template Thumbnail				| Rear Cover Plate Template							| - | - | - | 100% |  20g |
| Rear Cover Long 1.8" TFT with SD-Card Thumbnail				| Rear Cover Longer Version	for the 1.8" TFT with a SD-Card **(deprecated)**		| 1 | - | 1 | 100% |  63g |
| Rear Cover Long 1.77" TFT Thumbnail				| Rear Cover Longer Version	for the 1.77" TFT without a SD-Card	**(deprecated)**	| 1 | - | 1 | 100% |  63g |
| Rear Cover 1.77" TFT Thumbnail											| Rear Cover for the 1.77" TFT without a SD-Card **(deprecated)**						| 1 | - | 1 | 100% |  53g |
| Rear Cover Template Thumbnail						| Rear Cover Template				| - | - | - | - | - |
| Top Cover Split Front Thumbnail						| Top Cover Split Front				| 1 | - | 1 | 100% |  48g |
| Top Cover Split Rear Thumbnail						| Top Cover Split Rear **(deprecated)**	| 1 | - | 1 | 100% |  28g |
| Top Cover Split Rear Thumbnail				| Top Cover Split Rear with OLED	| 1 | - | 1 | 100% |  28g |
| Top Cover Template Thumbnail						| Top Cover Template				| - | - | - | - | - |
| Bottom Cover Split Front Thumbnail				| Bottom Cover Split Front			| 1 | - | 1 | 100% |  46g |
| Bottom Cover Split Rear Thumbnail					| Bottom Cover Split Rear			| 1 | - | 1 | 100% |  26g |
| Bottom Cover Template Thumbnail					| Bottom Cover Template				| - | - | - | - | - |

### Miscellanious

| Thumbnail | Name | normal copies | mirrored copies | total amount | infill | total weight |
|---|---|---|---|---|---|---|
| Servohorn 6 B-Star with 25 teeth for 20mm Servos		| Servohorn 6 B-Star				| 12 | - | 12 |  20% |  20g |

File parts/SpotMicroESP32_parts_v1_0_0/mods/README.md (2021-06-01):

# Available Mods
This section gives an overview of all available, publicly shared modifications i am aware of. I cannot guarantee for compatibility of functions -  please consider all of these experimental.

## Internal Links
These Mods are available in this repo. If you have your own mods you would like to share here, than please make a pull request.  

| Name | Description | Author | Source |
|---|---|---|---|
| Raspeberry Pi Zero Circuitry Mountingplate | Experimental Circuitry Mountingplate for Raspberry Pi Zero. It is untested and i cant determin if the wiring actually would work on the RPi Zero the same as on the ESP32 | Michael Kubina | https://github.com/michaelkubina/SpotMicroESP32/blob/master/parts/SpotMicroESP32_parts_v1_0_0/mods/rpi_zero_mountingplate |
| Silicone Foot Mould| A mould for casting the foot out of silicone. Screws and butterfly-nuts needed. Check this french video for informations on how to perform a silicone cast: https://www.youtube.com/watch?v=EenYul9Q1JI | Barbak13 (Discord) | https://github.com/michaelkubina/SpotMicroESP32/blob/master/parts/SpotMicroESP32_parts_v1_0_0/mods/silicone_foot_mould |
| Metaldisc Servorhorn Mod| Use Metaldisc Servohorns instead of the 6B-Star plastic servohorns | Edo (Discord) | https://github.com/michaelkubina/SpotMicroESP32/blob/master/parts/SpotMicroESP32_parts_v1_0_0/mods/metaldisc_servohorn_mod |
| Neopixel-Ring (55mm inner diameter) adapter plate| Adapter plate to be screwed beneath the screwholes in the top case, to fit a neopixel ring with an inner diameter of 55mm. FreeCAD-Files for custom modifications available. | Michael Kubina | https://github.com/michaelkubina/SpotMicroESP32/blob/master/parts/SpotMicroESP32_parts_v1_0_0/mods/neopixel_ring_55mm_adapter |

## External Links
These Mods are available through other sources.

| Name | Description | Author | Source |
|---|---|---|---|
| SpotMicroESP32 M3 Mod | Modded SpotMicroESP that uses only M3 screws | Projunk (Thingiverse) | https://www.thingiverse.com/thing:4575753 |
| SpotMicroESP32 Parametric Stand | A Stand to place your SpotMicroESP32 on | Projunk (Thingiverse) | https://www.thingiverse.com/thing:4604862 |
| SpotMicroESP32 Parametric Shoulder Reinforcement | A reinforcement mod to give the shoulders and therefore the servos more stability | Projunk (Thingiverse) | https://www.thingiverse.com/thing:4817676 |
| SpotMicroESP32 Parametric Shoulder Reinforcement with metaldisc servohorn mod | A mod of the reinforced shoulders mod, that uses the metaldisc servohorn instead of the 6B-Star | omtek (modulo1) (Discord) | https://www.thingiverse.com/thing:4873790 |

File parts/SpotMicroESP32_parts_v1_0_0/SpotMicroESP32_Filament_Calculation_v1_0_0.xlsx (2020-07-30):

Chassis & Shoulders
Amount | Part | Infill | Duration | Filament |  | Sum Duration | Sum Filament
2x | Inner Shoulder | 20% | 1h 29min | 16 | g | 2h 58min | 32 | g
2x | Outer Shoulder | 20% | 1h 33min | 16 | g | 3h 6min | 32 | g
2x | Bottom Shoulder | 20% | 36min | 6 | g | 1h 12min | 12 | g
2x | Top Shoulder | 20% | 54min | 10 | g | 1h 48min | 20 | g
2x | Chassis Side | 20% | 1h 7min | 11 | g | 2h 14min | 22 | g
1x | Circuitboard Mount | 20% | 2h 42min | 30 | g | 2h 42min | 30 | g
 |  |  |  |  |  | Total | 148 | g
Shoulder Joint
Amount | Part | Infill | Duration | Filament |  | Sum Duration | Sum Filament
4x | Shoulder Joint Servomount | 20% | 1h 10min | 12 | g | 4h 40min | 48 | g
4x | Shoulder Joint Servohorn Cap | 20% | 41min | 7 | g | 2h 44min | 28 | g
4x | Shoulder Joint Ball Bearing Pin | 20% | 5min | 0 | g | 20min | 0 | g
 |  |  |  |  |  | Total | 76 | g
Limb
Amount | Part | Infill | Duration | Filament |  | Sum Duration | Sum Filament
4x | Limb_Bottom_Shell | 20% | 2h 10min | 25 | g | 8h 40min | 100 | g
4x | Limb_Top_Shell | 20% | 2h 7min | 23 | g | 8h 28min | 92 | g
4x | Limb_Ball_Bearing_Mount | 20% | 29min | 5 | g | 1h 56min | 20 | g
4x | Limb_Servohorn_Mount | 20% | 31min | 5 | g | 2h 4min | 20 | g
 |  |  |  |  |  | Total | 232 | g
Foot
Amount | Part | Infill | Duration | Filament |  | Sum Duration | Sum Filament
4x | Wrist | 20% | 2h 1min | 26 | g | 8h 4min | 104 | g
4x | Wrist Counterpart | 20% | 47min | 9 | g | 3h 8min | 36 | g
4x | Shoulder Joint Ball Bearing Pin | 20% | 5min | 0 | g | 20min | 0 | g
4x | Foot Tip | 20% | 51min | 6 | g | 51min | 24 | g
 |  |  |  |  |  | Total | 164 | g
Covers
Amount | Part | Infill | Duration | Filament |  | Sum Duration | Sum Filament
1x | Front_Cover | 100% | 6h 2min | 63 | g | 6h 2min | 63 | g
1x | Rear_Cover | 100% | 4h 37min | 53 | g | 4h 37min | 53 | g
1x | Top_Cover_Split_Front | 100% | 4h 3min | 48 | g | 4h 3min | 48 | g
1x | Top_Cover_Split_Rear | 100% | 2h 21min | 28 | g | 2h 21min | 28 | g
1x | Bottom_Cover_Split_Front | 100% | 3h 53min | 46 | g | 3h 53min | 46 | g
1x | Bottom_Cover_Split_Rear | 100% | 2h 14min | 26 | g | 2h 14min | 26 | g
 |  |  |  |  |  | Total | 264 | g
 |  |  |  |  |  | Total Black PLA | 364
 |  |  |  |  |  | Total White PLA | 496
 |  |  |  |  |  | Total TPU | 24
 |  |  |  |  |  | Total Filament | 884

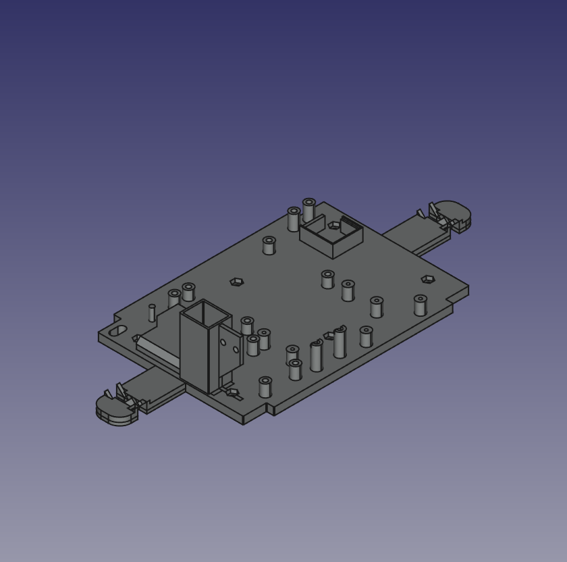
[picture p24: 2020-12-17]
parts/SpotMicroESP32_parts_v1_0_0/images/original/Circuitry_Mountingplate_SZBK07_Extended.png

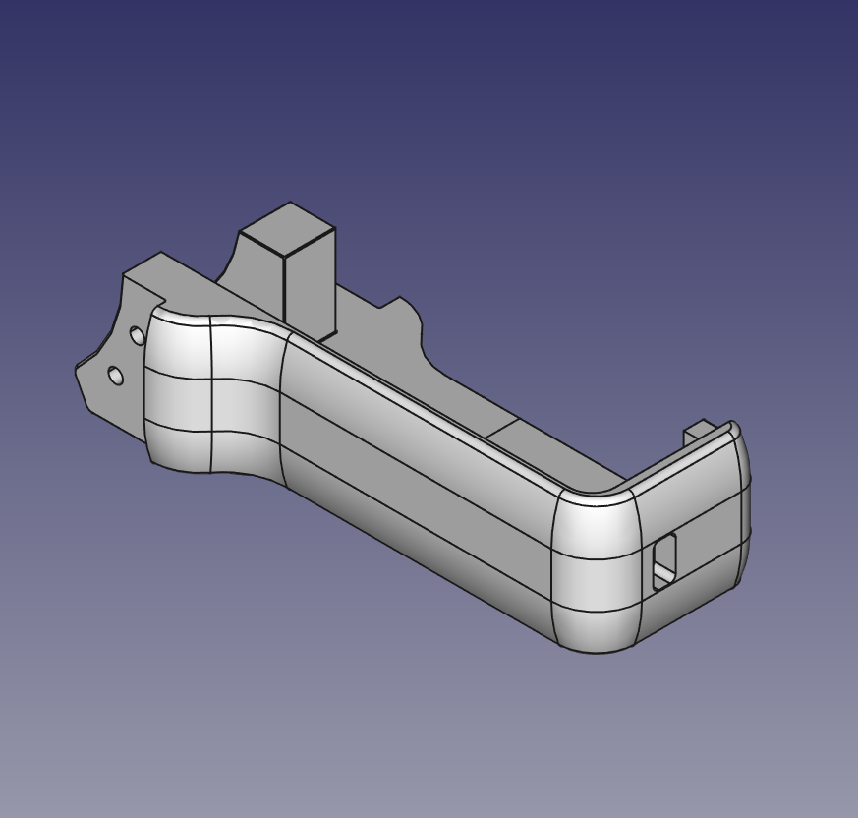
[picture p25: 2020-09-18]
parts/SpotMicroESP32_parts_v1_0_0/images/original/Limb_Top_Shell.png

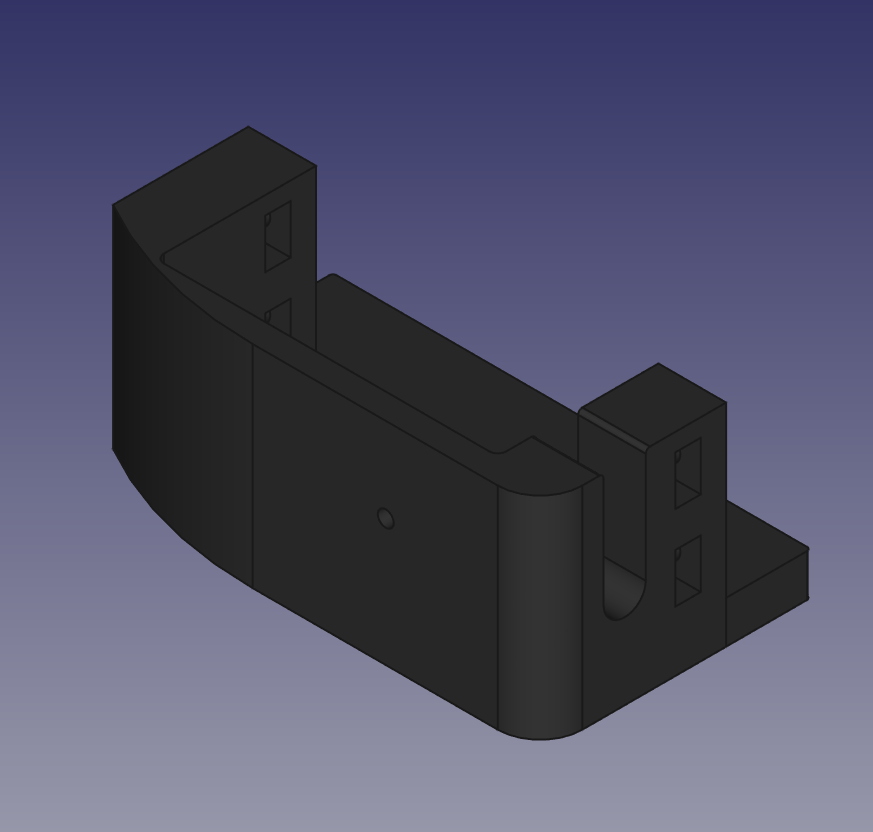
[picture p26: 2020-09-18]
parts/SpotMicroESP32_parts_v1_0_0/images/original/Wrist _Counterpart.png

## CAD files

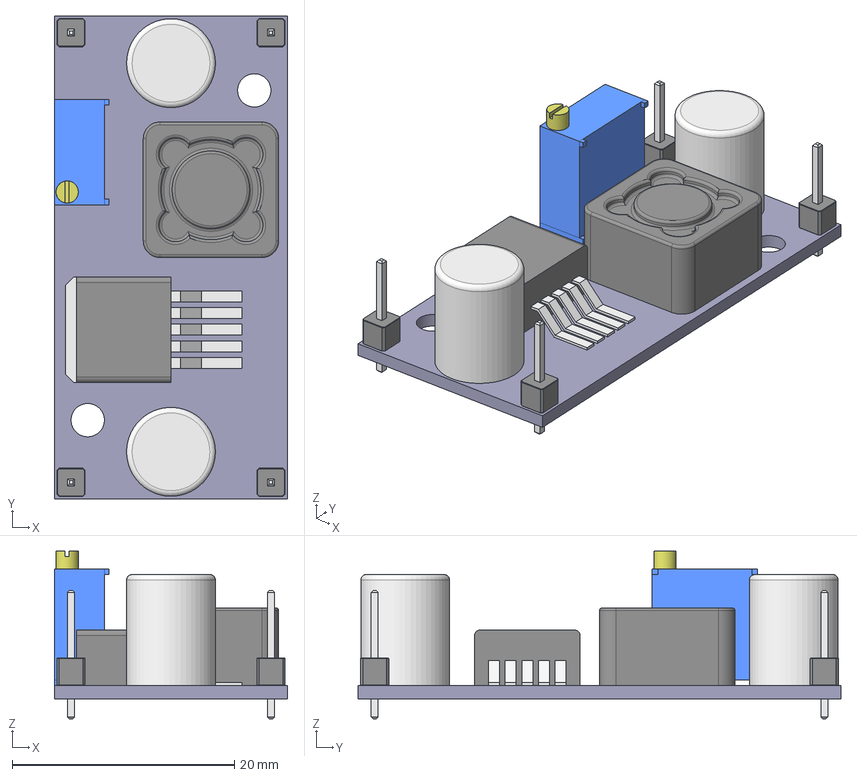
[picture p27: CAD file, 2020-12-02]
electronics/parts/LM2596S.FCStd
21.0 x 43.5 x 15.1 mm
LM2596S DC Converter PCB
Capacitor #1
Capacitor #2
Screwhead
Coil
LM2596S Body
Thermal
Pin Header Block001
Pin Header Pin001
Pin Header Block002
Pin Header Pin002
Pin Header Block003
Pin Header Pin003
Pin Header Block004
Pin Header Pin004

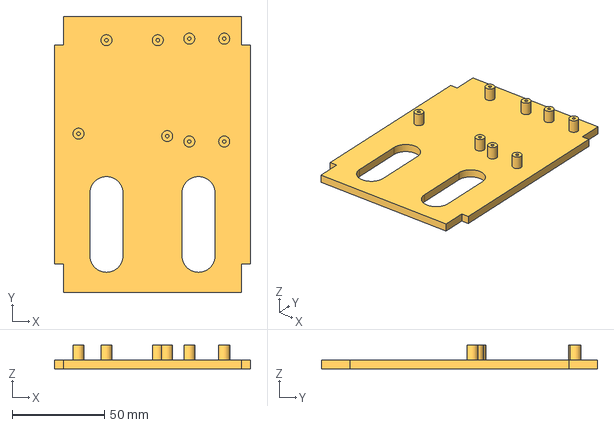
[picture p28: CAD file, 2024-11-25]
parts/SpotMicroESP32_parts_v1_0_0/freecad/Circuitry_Mountingplate_Arduino.FCStd
106.5 x 150.0 x 13.0 mm

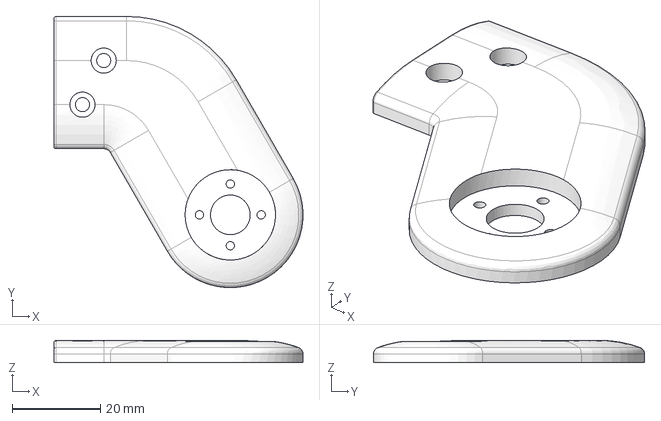
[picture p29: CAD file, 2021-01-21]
parts/SpotMicroESP32_parts_v1_0_0/mods/metaldisc_servohorn_mod/Limb_Servohorn_Mount_long_v5_circle_horn.step
56.5 x 61.5 x 5.00 mm

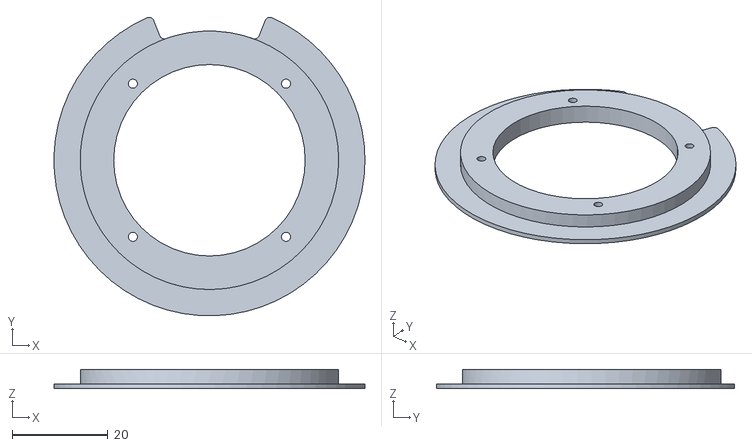
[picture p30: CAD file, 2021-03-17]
parts/SpotMicroESP32_parts_v1_0_0/mods/neopixel_ring_55mm_adapter/Led_Ring_Adatper_Prototype.stl
65.0 x 62.4 x 4.00

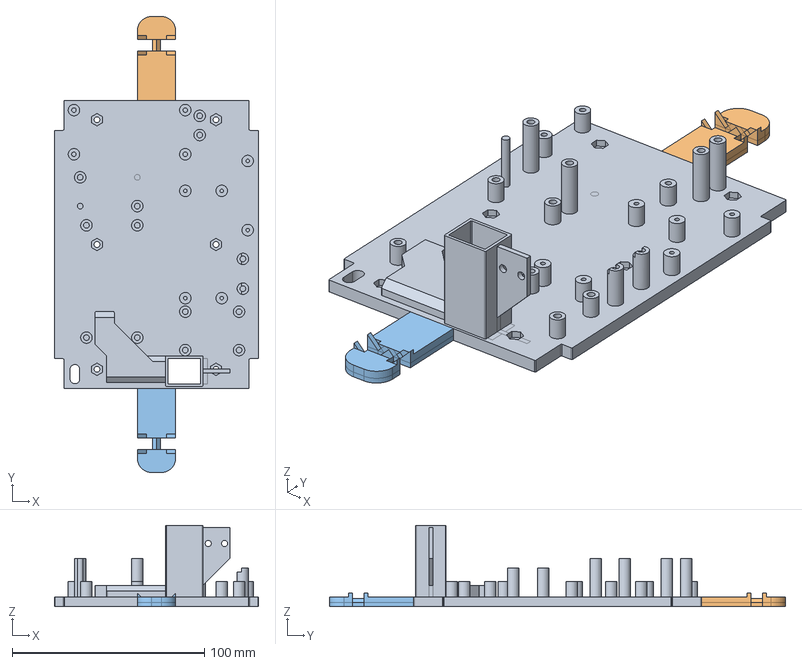
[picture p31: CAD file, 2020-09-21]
parts/SpotMicroESP32_parts_v1_0_0/mods/rpi_zero_mountingplate/EXPERIMENTAL_Circuitry_Mountingplate_Extended_Raspberry_Pi_Zero_W.FCStd
106.5 x 237.5 x 42.2 mm
Circuitry Mountingplate Base
Circuitry Mountingplate Front Extension
Circuitry Mountingplate Rear Extension

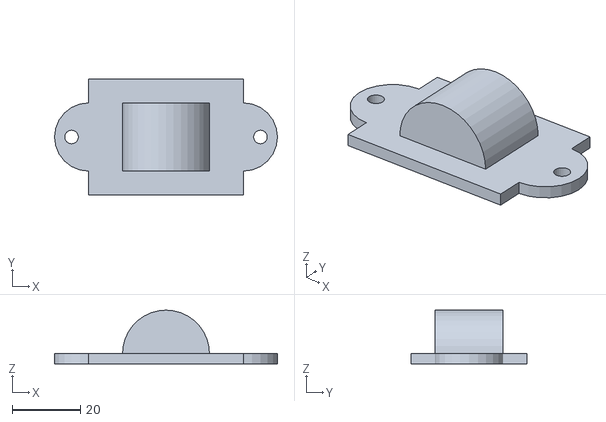
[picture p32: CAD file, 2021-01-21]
parts/SpotMicroESP32_parts_v1_0_0/mods/silicone_foot_mould/Moule_part2.stl
65.4 x 34.0 x 15.7

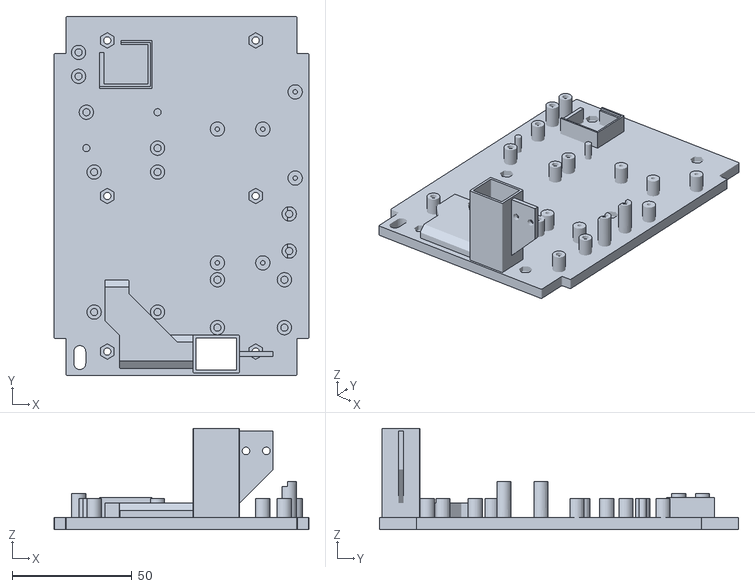
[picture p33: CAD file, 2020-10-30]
parts/SpotMicroESP32_parts_v1_0_0/stl/Circuitry_Mountingplate_XL4016.stl
106.5 x 150.0 x 42.2

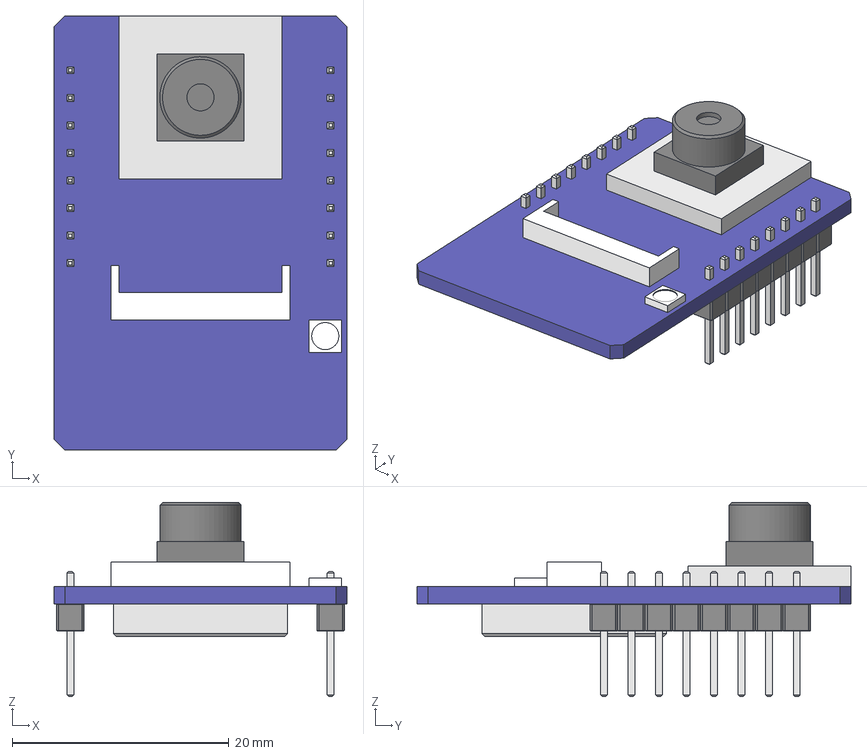
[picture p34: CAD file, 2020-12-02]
electronics/parts/ESP32-CAM_OV2640_v2.FCStd
27.0 x 40.0 x 17.9 mm
ESP32-CAM PCB
ESP32-CAM Flashlight
ESP32-CAM Camera
ESP32-CAM Metalplates
ESP32-CAM Cableconnector
ESP32-CAM ESP-Chip

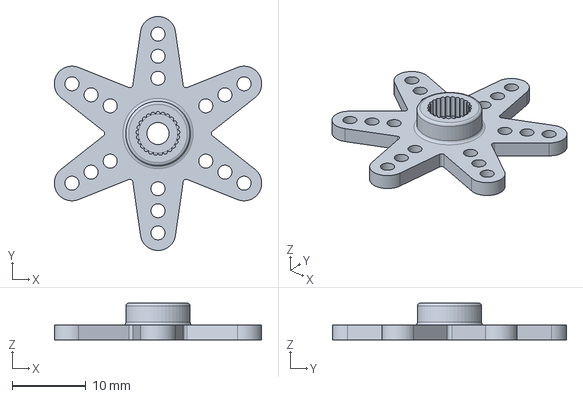
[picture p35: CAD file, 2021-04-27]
parts/SpotMicroESP32_parts_v1_0_0/freecad/Servohorn_6_B_Star.FCStd
28.2 x 31.8 x 5.00 mm

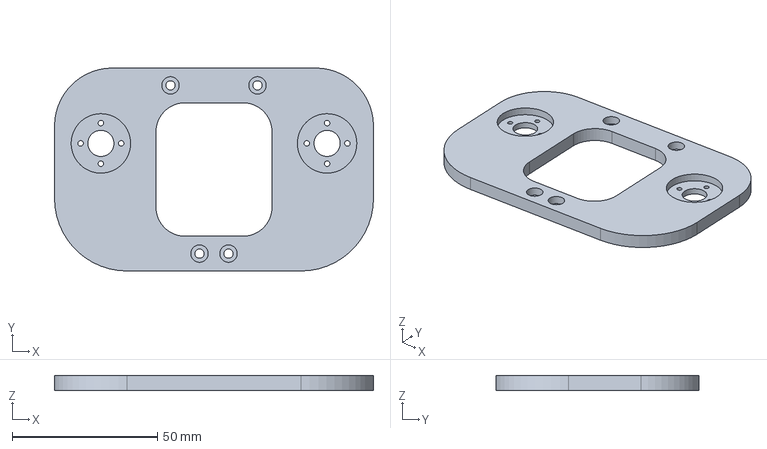
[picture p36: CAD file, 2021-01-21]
parts/SpotMicroESP32_parts_v1_0_0/mods/metaldisc_servohorn_mod/Outer_Shoulder_circle_horn.step
110.0 x 70.0 x 5.00 mm

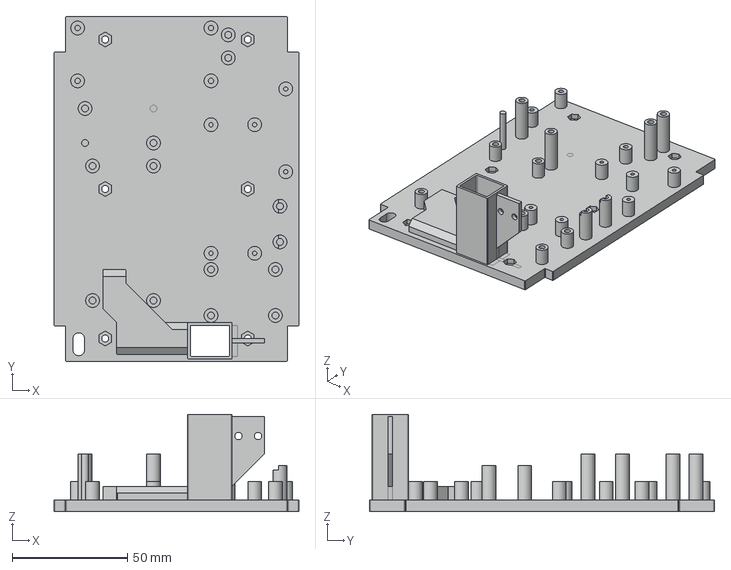
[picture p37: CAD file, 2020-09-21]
parts/SpotMicroESP32_parts_v1_0_0/mods/rpi_zero_mountingplate/EXPERIMENTAL_Circuitry_Mountingplate_Raspberry_Pi_Zero_W.FCStd
106.5 x 150.0 x 42.2 mm

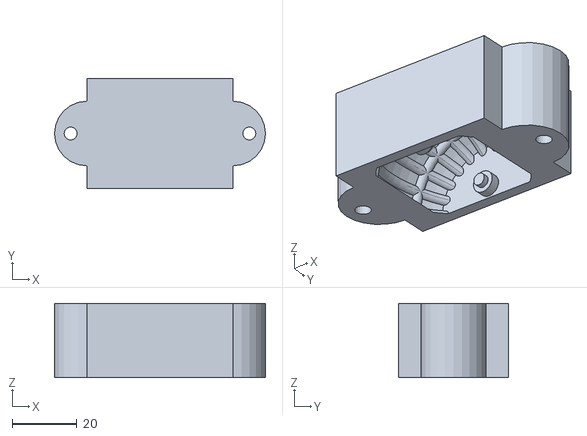
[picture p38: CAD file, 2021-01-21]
parts/SpotMicroESP32_parts_v1_0_0/mods/silicone_foot_mould/Moule_part1.stl
65.4 x 34.0 x 23.0

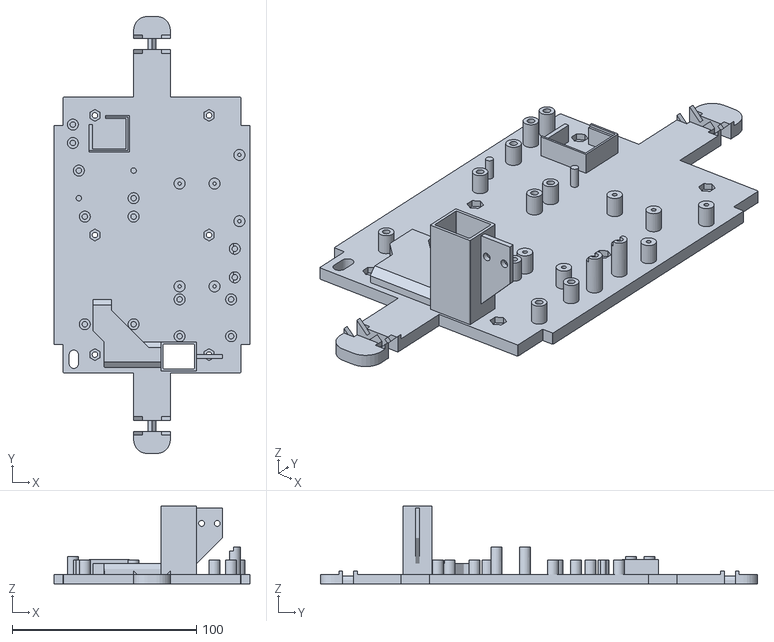
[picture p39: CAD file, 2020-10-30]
parts/SpotMicroESP32_parts_v1_0_0/stl/Circuitry_Mountingplate_XL4016_Extended.stl
106.5 x 237.5 x 42.2

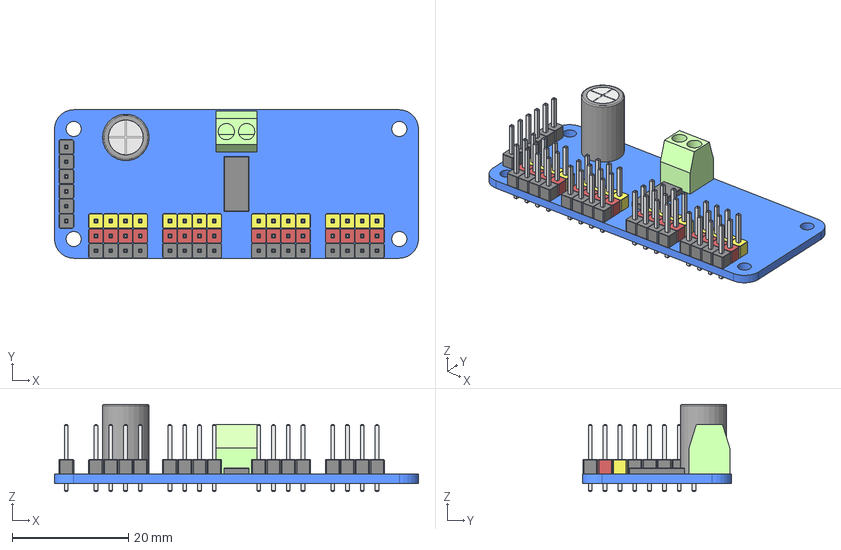
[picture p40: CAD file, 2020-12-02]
electronics/parts/PCA9685_servoboard.FCStd
62.5 x 25.5 x 15.0 mm
PCA9685 PCB
Terminal Block
PCA9685
Capacitor Body
Capacitor Head

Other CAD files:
parts/SpotMicroESP32_parts_v1_0_0/mods/neopixel_ring_55mm_adapter/LED_RING_ADAPTER_PROTOTYPE.FCStd
parts/SpotMicroESP32_parts_v1_0_0/freecad/Circuitboard_Mount (Template).FCStd
parts/SpotMicroESP32_parts_v1_0_0/mods/metaldisc_servohorn_mod/Shoulder_Joint_Servohorn_Cap_circle_horn.step
electronics/parts/GY-521.FCStd
electronics/parts/0_96_inch_I2C_OLED.FCStd
electronics/parts/ESP32_Devkit_C.FCStd
electronics/parts/ESP32_Devkit_C_v4.FCStd
electronics/parts/HW-482_KY-019.FCStd
electronics/parts/MG996R.FCStd
electronics/parts/SZBK07.FCStd
electronics/parts/USB-PORT.FCStd
electronics/parts/XL4016_DCDC_Converter.FCStd
electronics/parts/deprecated/1_8_inch_tft_screen.FCStd
electronics/parts/deprecated/1_8_inch_tft_screen_with_sd_card.FCStd
electronics/parts/neopixel_rgb_ring_5cm.FCStd
electronics/parts/pushbutton_19mm.FCStd
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

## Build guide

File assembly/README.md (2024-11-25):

# Assembly #
This document describes the assembly process for the SpotMicroESP32. There are some prerequisites to make, before you can begin with the assembly of your printed parts and before you can mount your parts into place. Make sure you have the necessary parts from the [3D-printed Partlist](https://github.com/michaelkubina/SpotMicroESP32/blob/master/parts/SpotMicroESP32_parts_v1_0_0/). You will need at least the screws and nuts from the [Bill of Materials](https://github.com/michaelkubina/SpotMicroESP32#bill-of-material).

**Important! Read the assembly guide at least once, so you are familiar with when to use mirrored parts or which servo should be mounted with which actual gear-position.**

## Prerequisites ##
The single most important thing is to test and to calibrate your servos. By calibration i mean to determin the minimum and maximum positions, and what dutycicle results in what actual angle. Don't use any servos, that behave weird in any way, such as: stuttering, grinding noises, clicking noises or which wont turn at least full 180° - you would regret it afterwards and will have to do a lot of disassembling stuff to get it straight. At last it is important, that you position each servo into a specific position, which will be named in the parts-list in each major step. Depending on where it should be mounted, it results in 2x 0° 2x 60°, 2x 120°, 2x 180° and 4x 90°. Make sure you **add all the rubber dampeners** to your servos, so you could fit the M3 through the mounting holes.
If you wish to use fabric hoses, make sure you use the smallest and thinest possible. There is just not enough space in these parts to use thick ones. Or simply go with the standard servocable, which could look pretty nice, depending on your color theme.

### Servo Calibration ###

This section gives a brief explenation, of what is meant with servo calibration. You can use the values determined by this right away with [Maarten Weyns firmware](https://github.com/michaelkubina/SpotMicroESP32/tree/master/code#firmware-and-app-by-maarten-weyn).

The servos you buy have most likely a larger overall movement range than the stated 180° or 270°. When doing the calibration steps, we are interested in several things:

- what is the minimum pwm signal, at which the servo starts actually moving?
- what is the maximum pwm singal, at which the servos actually stops its movement?
- what is the overall angle the servohorn did rotate between the minimum and maximum pwm singals? (**overall** movement range)
- what range in the overall movement range should represent our wanted 180° movement range with its corresponding PWM-values? (movement range)
- what ratio is there between the pwm-range and the movement angle? (conversion factor)

#### Example ####

Lets say you have a servo and feed it manually PWM-values, that you can easily increasy by 5, 10, 50, 100 or so. Also you have added a servohorn that allows you to see how far it did rotate in degree. This allows for gathering all informations needed for this calibration:

At a hypothetical PWM-value at 12 Bit resolution at a PWM-frequency of *50Hz(!)*:
- at 0 to 74 nothing happens and the servohorn does not want to move at all
- at 75 your servohorn actually moves...and stops at a certain position -> this is the minimum position of its **overall** movement range
- at 275 your servohorn did move forward exactly a quarter rotation -> so seen from the minimum of the **overall** movement range we have now progressed 90° further
- at 475 your servorhorn did an additional quarter rotation -> so we have now progressed even 180°
- now you increase the PWM-value even more and you see, that up to 510 your servohorn still rotates...and it stops at around 195°
- 511 to 4095 nothing happens anymore

What is happening here?

You have determined, that the minimum PWM-value that does anything is at 75, the maximum PWM-value that does anything is at 510. This results in an **overall** movement range of 195°, which is (in this example) 15° more than the 180° from the datasheet. Within this **overall** range we can now pick a movement range of 180°. Conveniently we would give ourselves a buffer before and after it (because the **overall** movement range allows for it), thus making the golden middle our 90° mark (= 97,5° from the **overall** movement range) and calculating or (even better) testing for the 0°/180° marks seen from there - this could be something like a PWM-Value of 92 (=7,5° of the **overall** movement range) and 492 (=187.5° of the **overall** movement range). This buffer allows for accounting for wear-off of the servos by software, instead of disassembling the robot to get the servos straight again.

So this has already answered the first four questions, about the PWM-Values and the angles those set the servo to. The last quesion about the conversion factor is just some simple maths and gives the idea of how much PWM-value increase is needed to rotate the servohorn by 1°. Like this:

- (510-75)/195° = 2.23 (conversion factor)
- (2.23 x 7,5°) + 75 ~= 92 (0° mark with a buffer of 7,5° before)
- (2.23 x 7,5°) + 475 ~= 492 (180° mark with a buffer of 7,5° after)

## Wrist ##
You need to make two identical wrists each for both sides - this means, that you need two mirrored pieces for the wrist and wrist counterpiece. Its important that you extend the servo cable and if you use fabric hoses, to guide it through.

### Parts ###

| Total Amount | Part |
|---|---|
|  4x | MG996R (2x at 0° and 2x at 180°) |
| 16x | Servo rubber dampeners (should be shipped with your servo) |
|  |  |
|  |  |
|  4x | [Wrist](../parts/SpotMicroESP32_parts_v1_0_0/README.md#leg) (2x right-handed, 2x left-handed) |
|  4x | [Wrist counterpiece](../parts/SpotMicroESP32_parts_v1_0_0/README.md#leg) (2x right-handed, 2x left-handed) |
|  4x | [Shoulder Joint Ball Bearing Pin](../parts/SpotMicroESP32_parts_v1_0_0/README.md#leg) |
|  4x | [Foot Tip](../parts/SpotMicroESP32_parts_v1_0_0/README.md#leg) |
|  |  |
|  |  |
| 24x | M3 nuts |
| 16x | M3x20 |
|  8x | M3x8 |
|  4x | M2 nuts |
|  4x | M2x8 |

### Wrist and foot tip ###

Insert 2x M3 nuts into their spaces in the wrist. Hold the foot tip at position and screw with 2x M3x8 the foot tip into place.

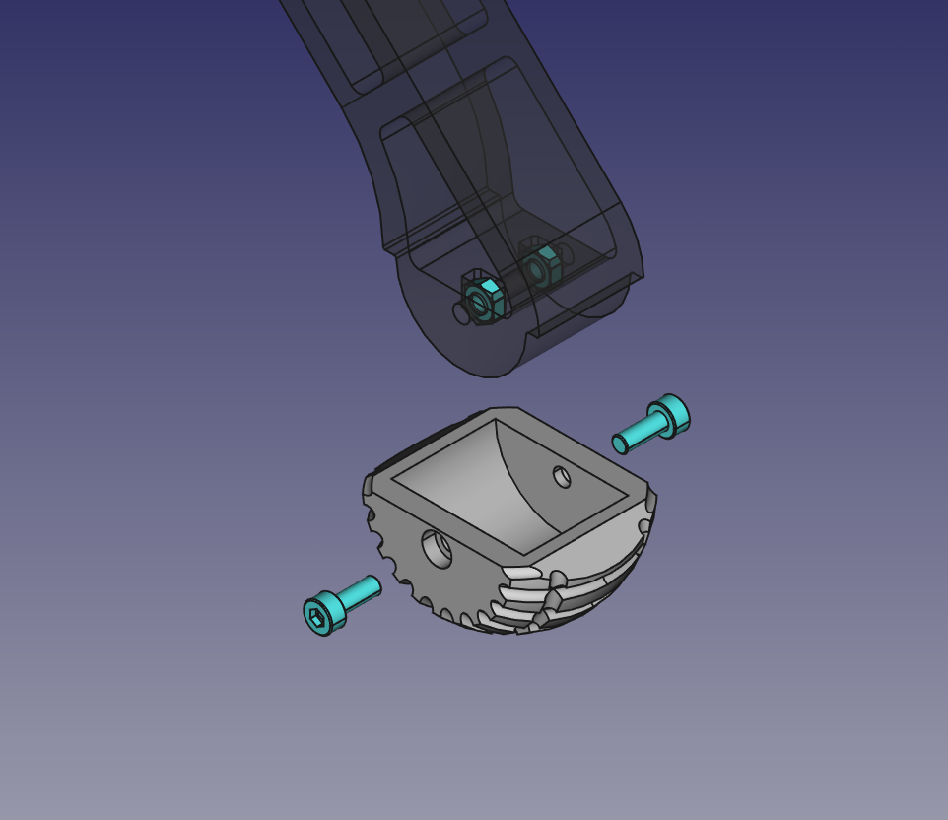
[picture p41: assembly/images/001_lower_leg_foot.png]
001 - Wrist & Foot Tip


### Wrist counterpiece and ball bearing pin ###

Insert 1x M2 nut into the small space in the wrist counterpiece. Screw 1x M2x8 through the ball bearing pin and attach it to the wrist counterpiece.

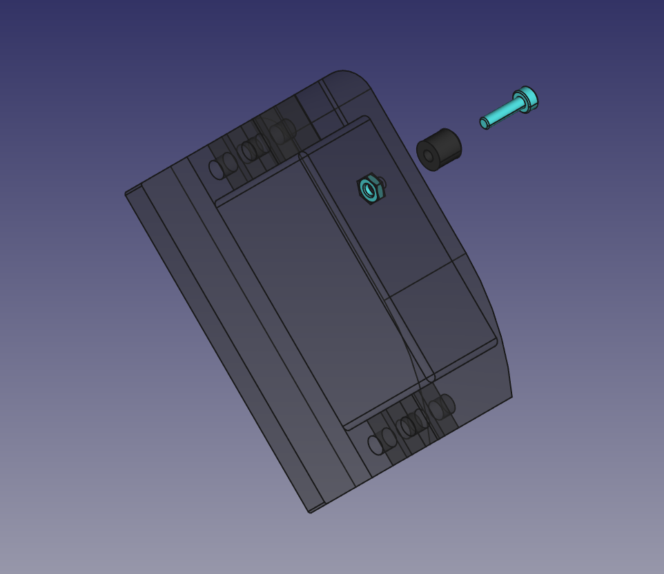
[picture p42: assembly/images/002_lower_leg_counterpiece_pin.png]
002 - Wrist Counterpiece & Ball Bearing Pin


### Wrist counterpiece and ball bearing pin ###

Insert 4x M3 nuts into the small spaces in the wrist counterpiece. Insert now from above the servo into its pocket in the wrist counterpiece. Now push both the wrist counterpiece with the servo and the wrist with the foot tip together, closing all gaps. Be careful not to loose any M3 nuts and screw both parts together with 4x M3x20 screws.

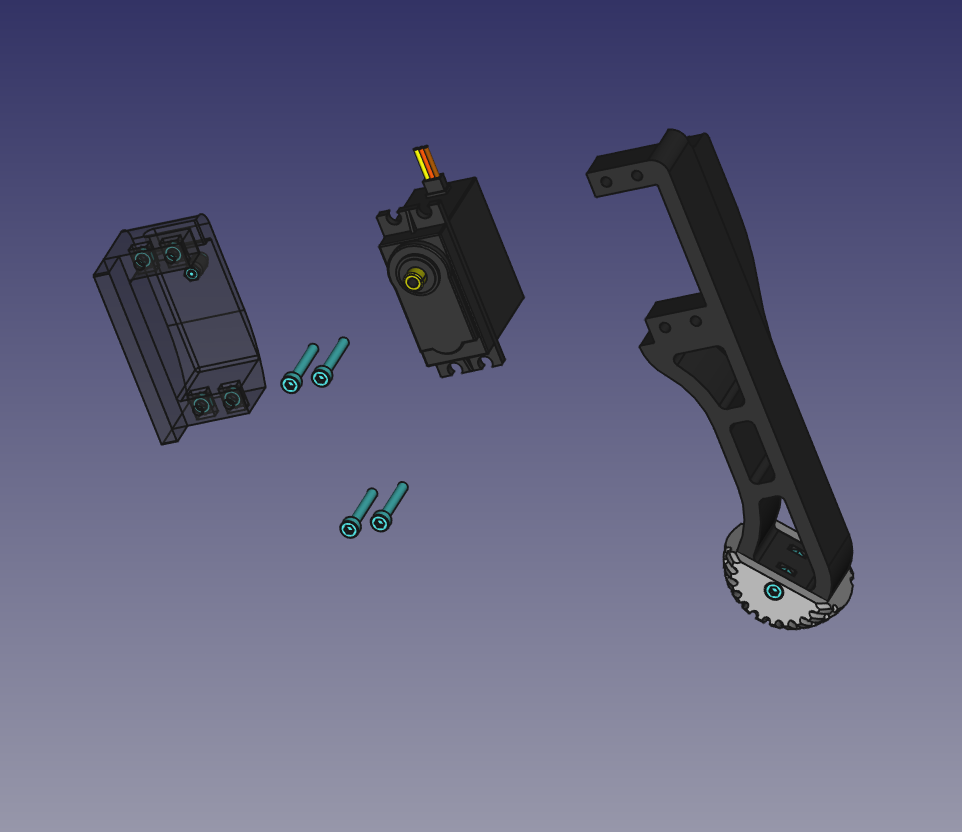
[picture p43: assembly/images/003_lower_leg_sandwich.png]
003 - Wrist Sandwich


### Wrist completed ###

Your assembled wrist should look like this one. Repeat it once again for the second left wrist and assemble the two mirrored (right-handed) right wrists.

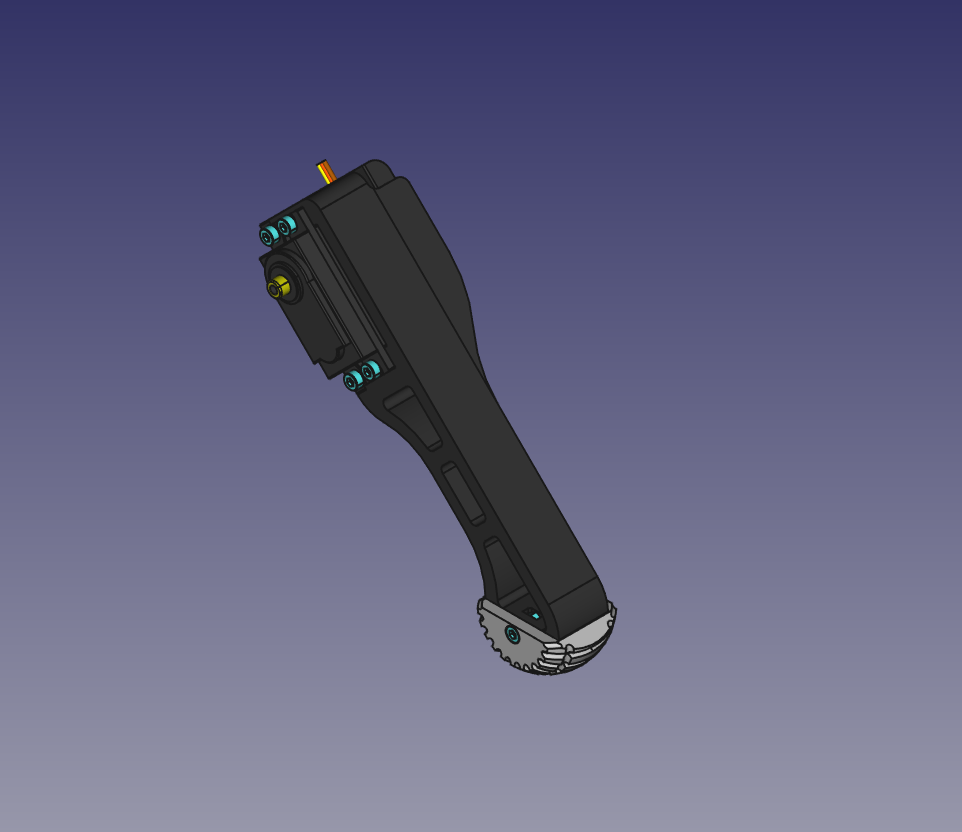
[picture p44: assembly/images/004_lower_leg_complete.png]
004 - Wrist Complete


## Upper Leg ##
You need to make two identical upper legs each for both sides - this means, that you need two mirrored pieces for the upper leg bottom shell, upper leg top shell, servohorn mount and ball bearing mount.

### Parts ###

**you might use only two M2x8 on each leg to screw the servohorn into place and thus reducing the amount of M2x8 screws and M2 nuts by 2/3**

**if you have M2x6 then use these instead of the M2x8 which are only in use, because it was easier to buy the screws and nuts in bulk**

**use the long version of the servohorn & ballbearing mount for improved resting position of the legs or stick to the normal version true to KDY-0523's design for the legs being at an angle when resting**

| Total Amount | Part |
|---|---|
|  4x | MG996R at 2x 60° and 2x 120° |
| 16x | Servo rubber dampeners (should be shipped with your servo) |
|  4x | FSH6S Servohorn |
|  4x | 625zz ball bearings without flange |
|  |  |
|  |  |
|  4x | [Limb Top Shell](../parts/SpotMicroESP32_parts_v1_0_0/README.md#leg) (2x right-handed, 2x left-handed) |
|  4x | [Limb Bottom Shell](../parts/SpotMicroESP32_parts_v1_0_0/README.md#leg) (2x right-handed, 2x left-handed) |
|  4x | [Limb Servohorn Mount](../parts/SpotMicroESP32_parts_v1_0_0/README.md#leg) **long version!** (2x right-handed, 2x left-handed) |
|  4x | [Limb Ball Bearing Mount](../parts/SpotMicroESP32_parts_v1_0_0/README.md#leg) **long version!** (2x right-handed, 2x left-handed) |
|  |  |
|  |  |
| 32x | M3 nuts |
| 32x | M3x20 |
|  4x | M3x8 |
| 24x | M2 nuts |
| 24x | M2x8 |

### Servohorn mount ###

You need to screw the M2 nuts on the M2x8 first, otherwise it would hinder the mounting of the servohorn. You can't use the bare M2x8 screws without the nuts in this step, because they would stick out from the other side and touch the servo unavoidably, which would result in blocking the servo movement or other damage. **You might consider using M2x6 instead and ditch the need for M2 nuts here completly.** Screw the servohorn into place, using the middle hole on each little arm. Make sure that the two arms of the servohorn are perfectly perpendicular to the wrist, when mounted to the servogear at 0° resp 180° (depending which leg) and which arm was on top then. This is because the teeth are not an even number and by this not symmetrical which would either result in a gap between the lower and upper leg when resting or in the worst case, the servo could not rest in 0° or 180° position and always stutter thus pulling more current. 

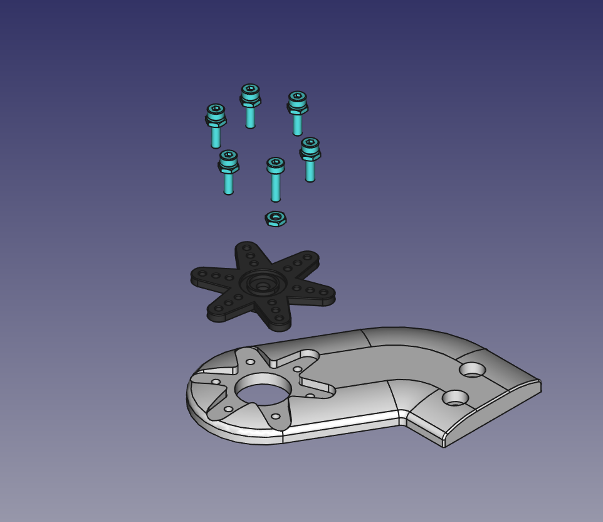
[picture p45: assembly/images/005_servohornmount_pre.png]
005 - Servohorn & Servohornmount


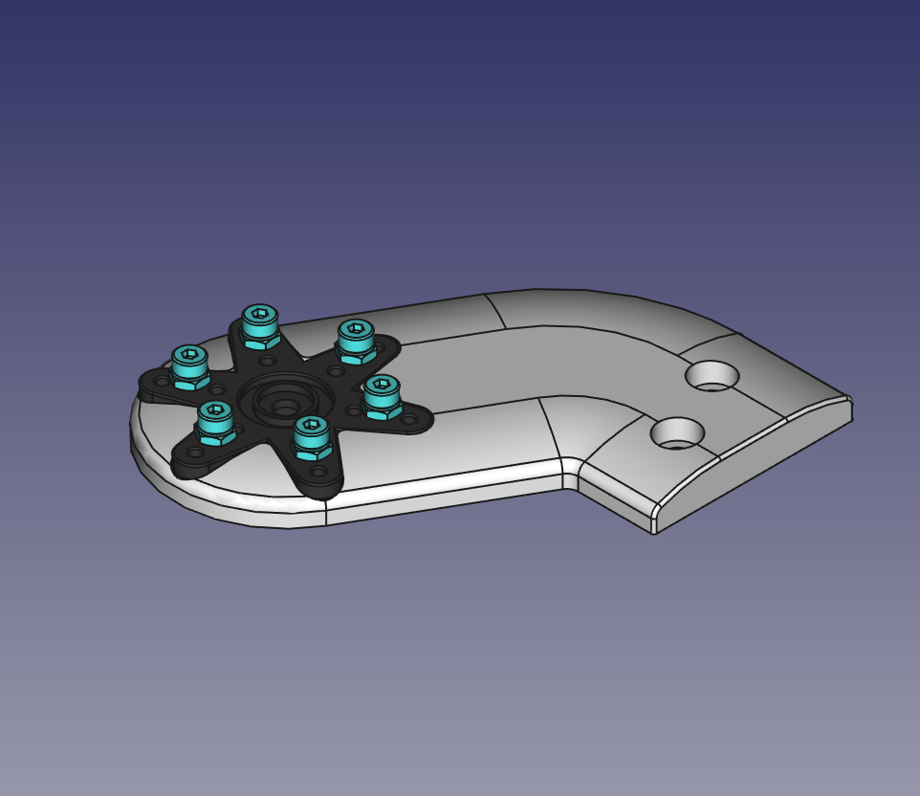
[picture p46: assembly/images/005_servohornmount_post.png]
005 - Servohorn & Servohornmount


### Attach Servohorn mount ###

Position the assembled servohorn mount to the wrist and make sure that the right arm ist on top. Otherwise remove the servohorn and turn it around as long as it sits perfectly perpendicular and attach it again. Screw the whole servohornmount with a M3x8 to the servo gear.

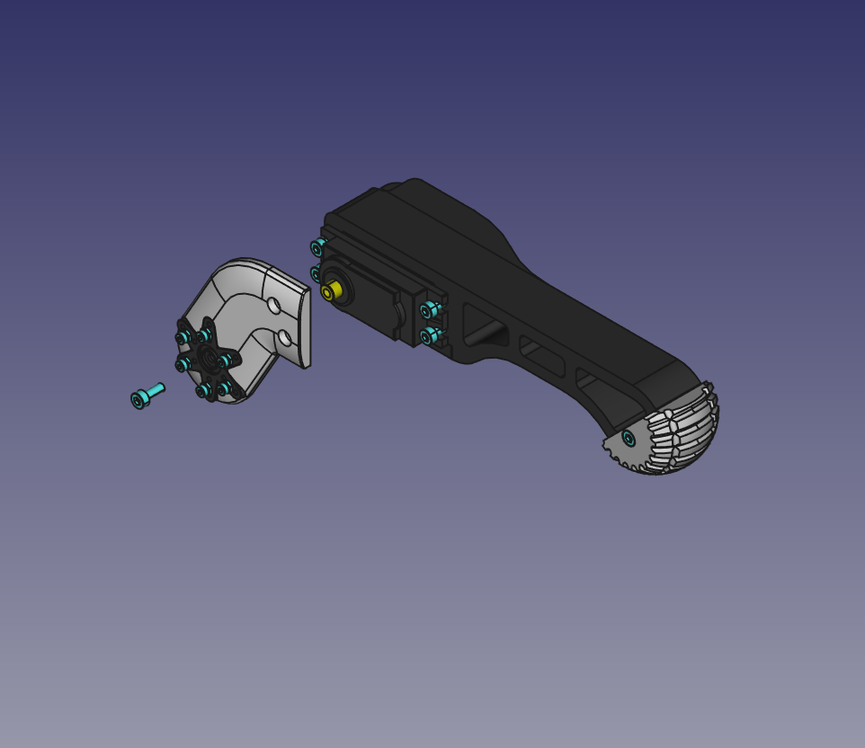
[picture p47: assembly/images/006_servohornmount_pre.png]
006 - Servohornmount & Servo Gear


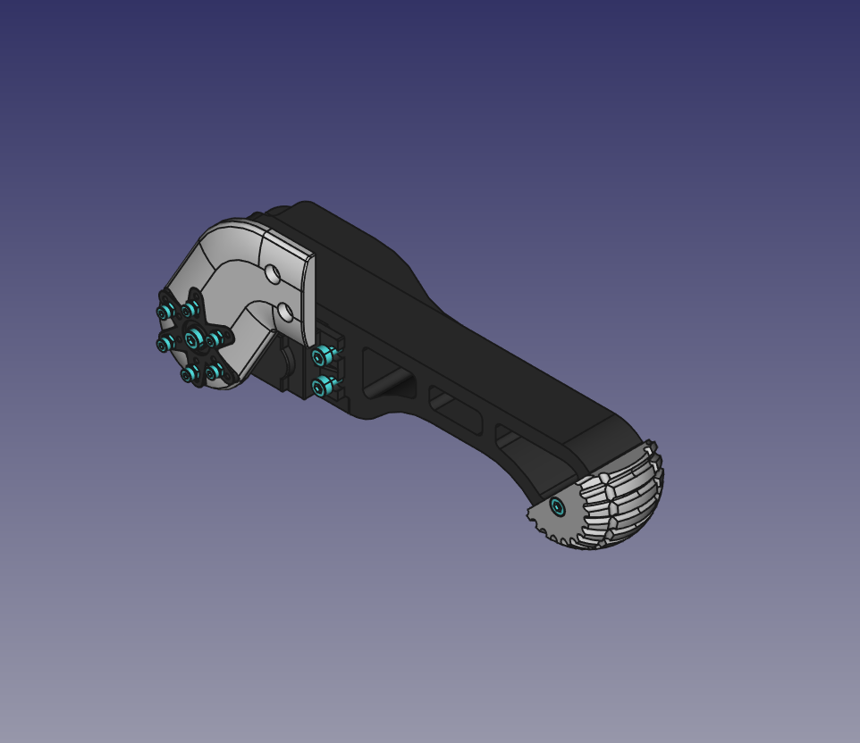
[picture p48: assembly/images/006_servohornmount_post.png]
006 - Servohornmount & Servo Gear


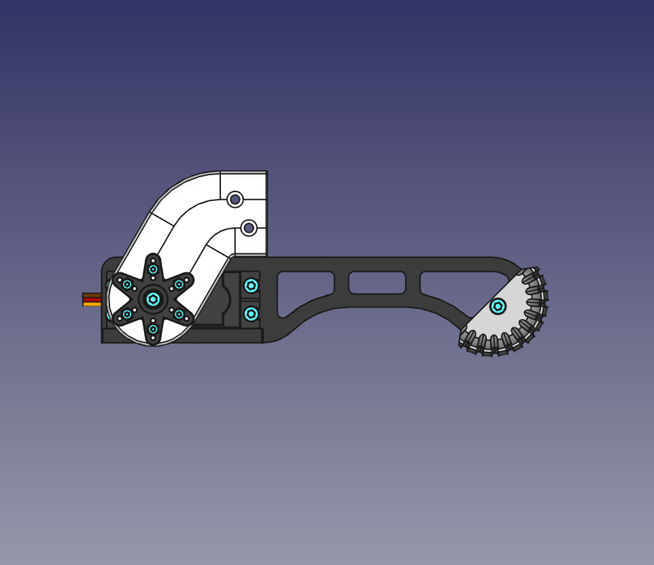
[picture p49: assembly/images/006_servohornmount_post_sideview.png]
006 - Servohornmount & Servo Gear


### Attach Ballbearing mount ###

Push your 625ZZ Ball Bearing into the Ballbearing Mount (it should be are really tight fit). Afterwards push the ballbearing mount on the ballbearing pin of the wrist.

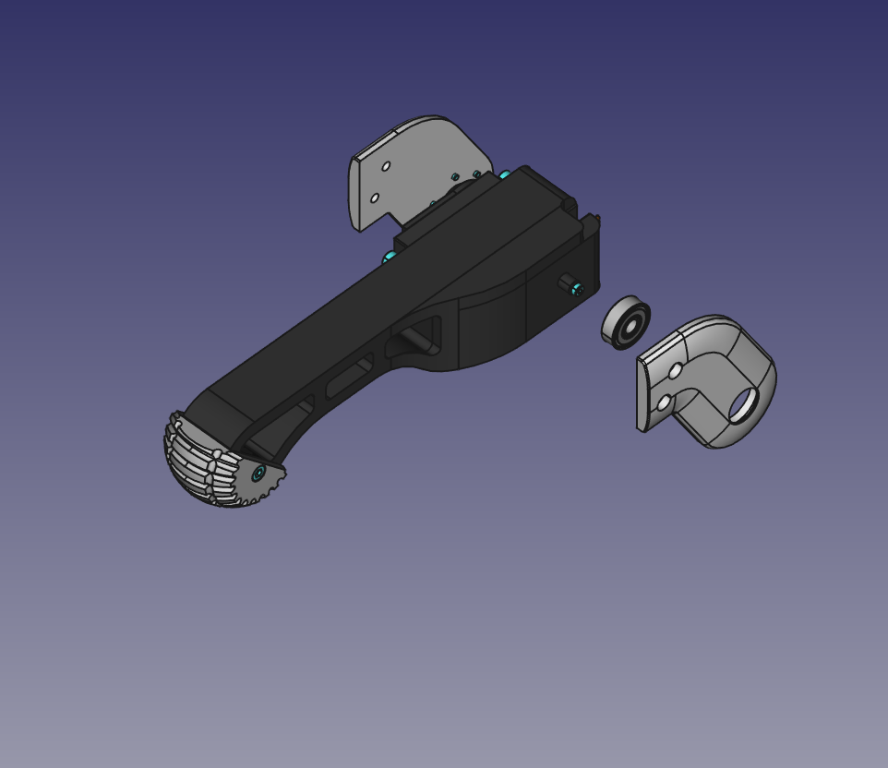
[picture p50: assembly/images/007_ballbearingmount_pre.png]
007 - Ballbearing mount


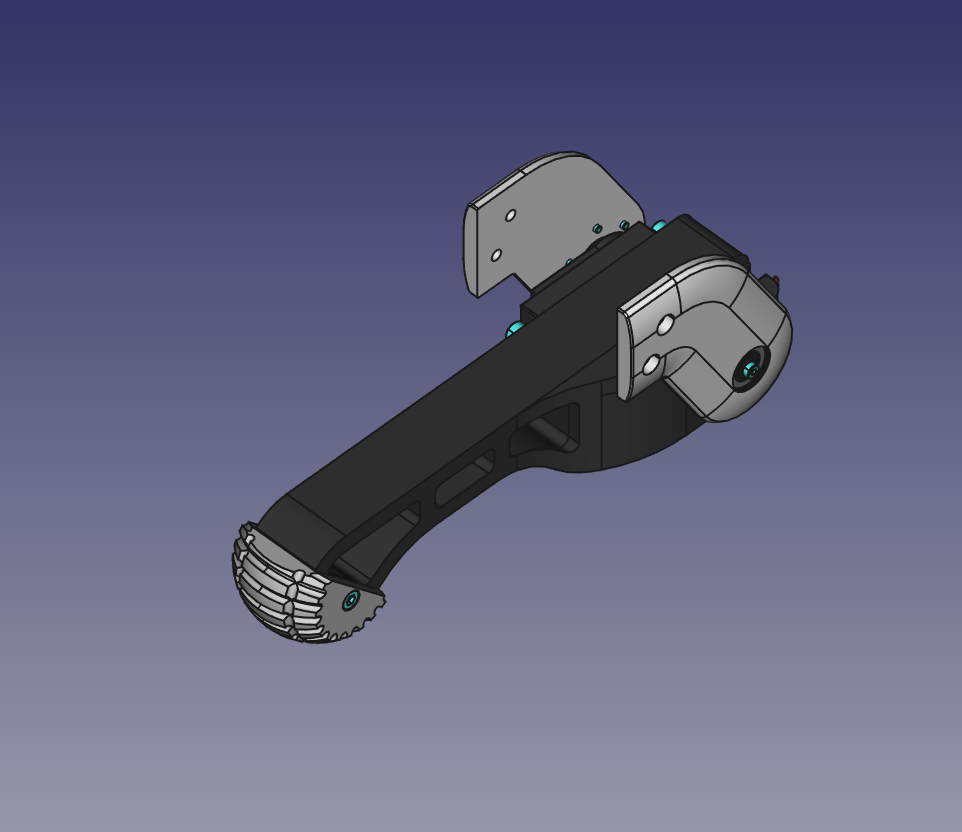
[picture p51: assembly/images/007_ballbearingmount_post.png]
007 - Ballbearing mount


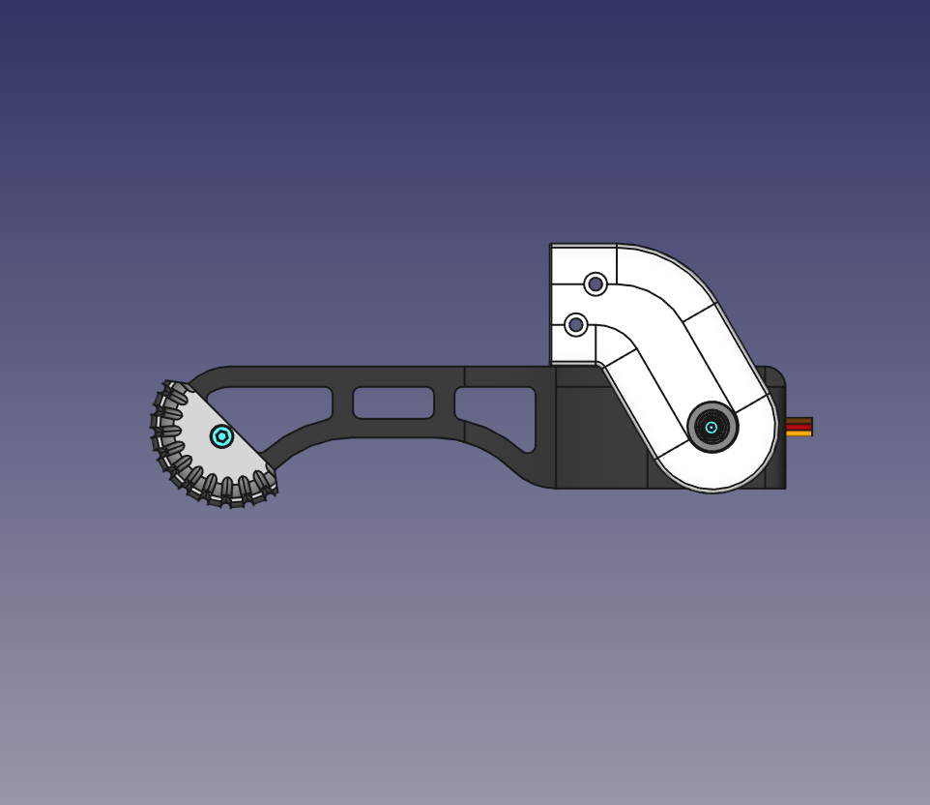
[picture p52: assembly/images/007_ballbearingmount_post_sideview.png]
007 - Ballbearing mount


### Upper Leg Bottom Shell preparation ###

Put four M3 nuts in the holes by the servo-pocket and push the servo into place. The two inner nuts are secured by the servo, the two out nuts might fall out so be careful not to lose them.

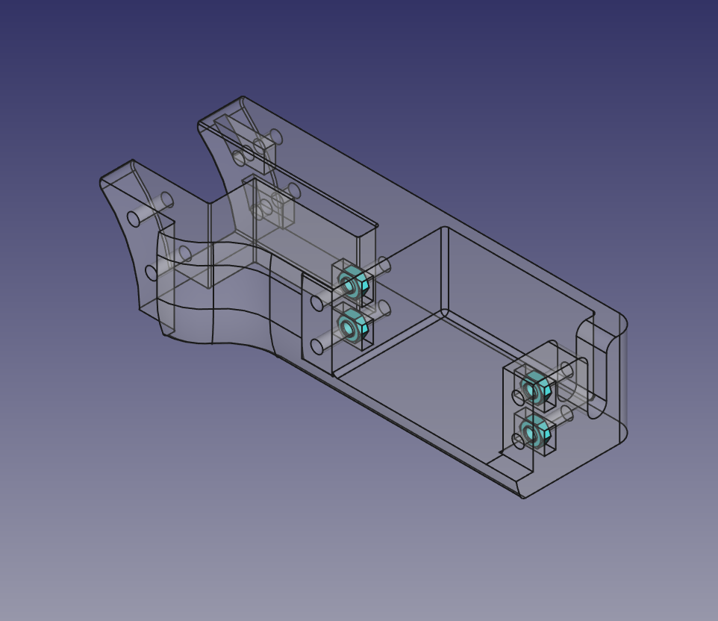
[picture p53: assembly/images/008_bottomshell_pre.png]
008 - Bottom Shell & Servo


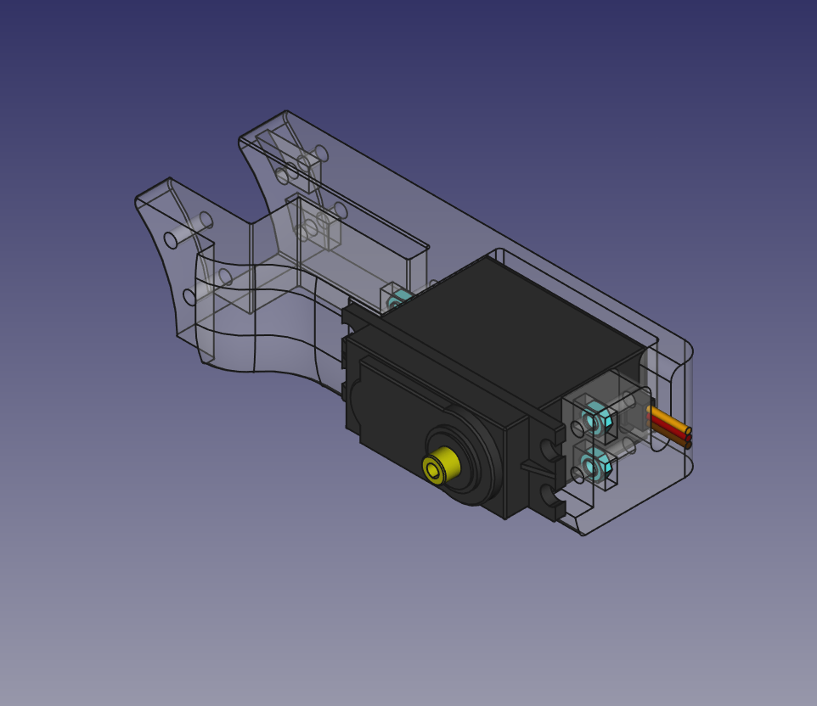
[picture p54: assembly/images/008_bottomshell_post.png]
008 - Bottom Shell & Servo


### Route Cables through Upper Leg Top Shell ###

This part is a bit tricky, especialy when using fabric hoses for the servocables, since the space between the shells is very limited. Route your extended servocable from the wrist through the front hole of the top shell. Pull after that the servocable of the bottom shell servo through the hole as well. 

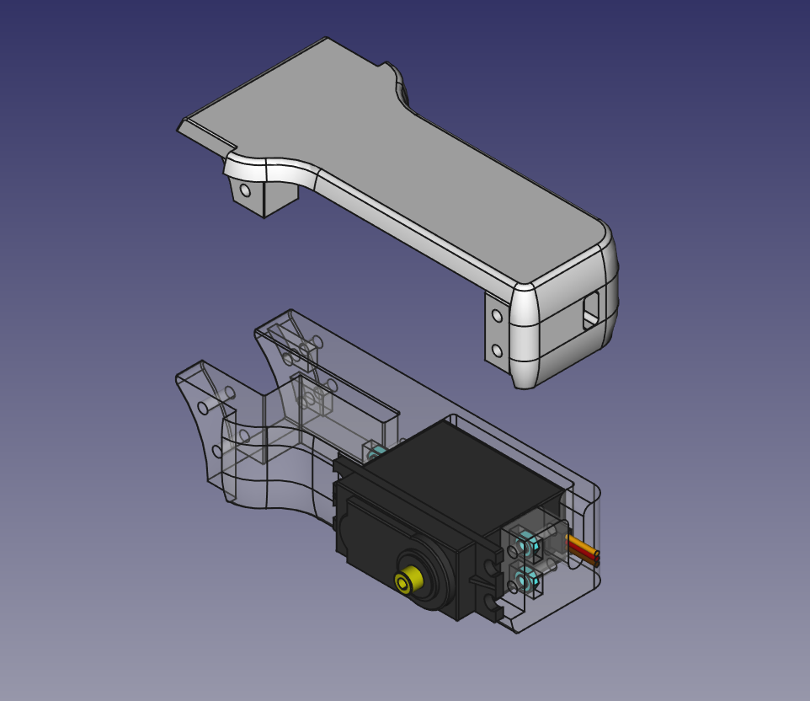
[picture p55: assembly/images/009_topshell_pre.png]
009 - Top Shell & Bottom Shell


Then push both shells toghether and at the same time pull the cables carfully further through the hole. Make sure the servocable from the wrist goes into both shells through the gap between both shells and is further guided underneath the top shell in the groove specially made for it (marked green). You have also to watch out not to lose the two M3 nuts next to the servo.

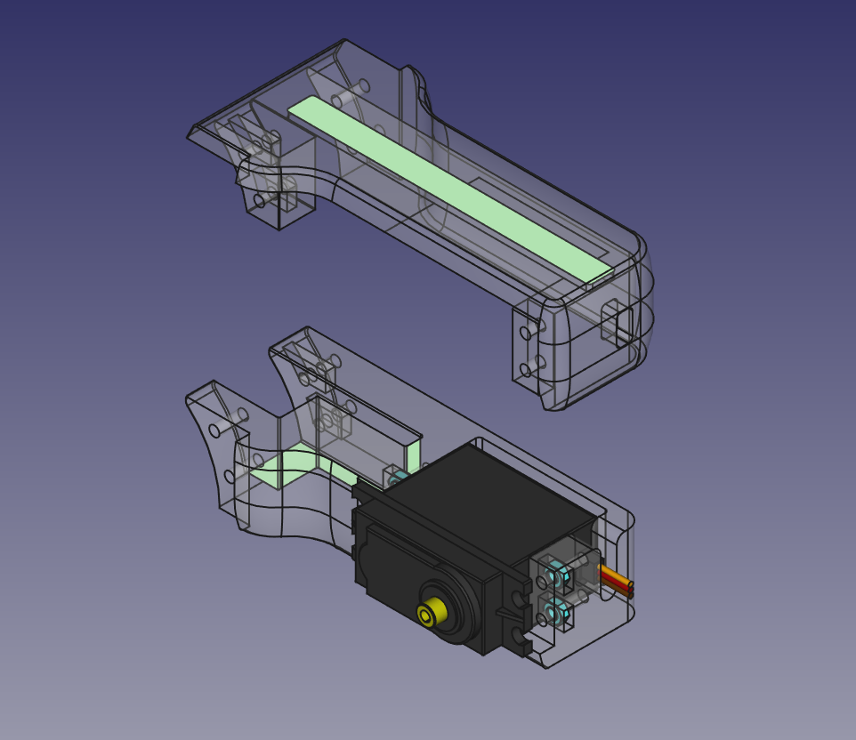
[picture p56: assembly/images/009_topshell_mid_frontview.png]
009 - Top Shell & Bottom Shell


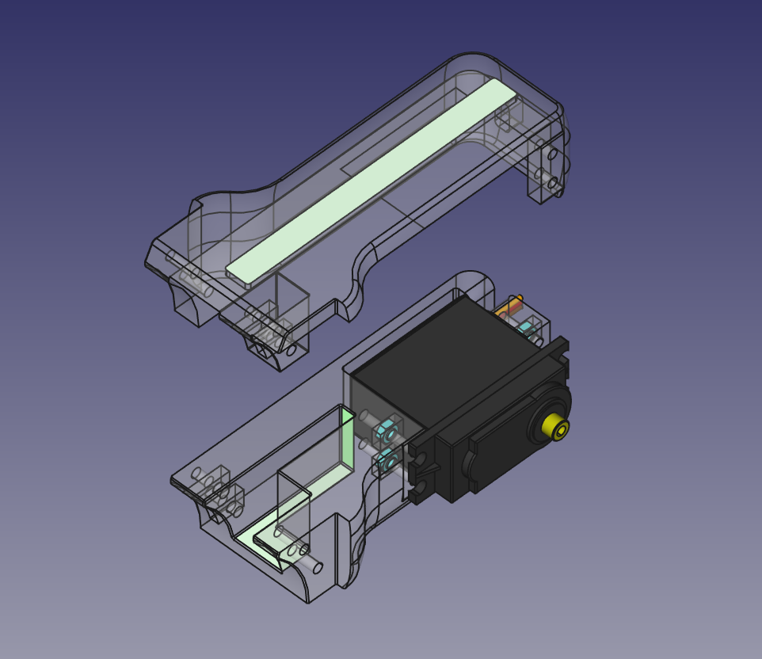
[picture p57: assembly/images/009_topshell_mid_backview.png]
009 - Top Shell & Bottom Shell


### Screw both shells together ###

When both shells are closed you might either move your cables freely back and forth through the hole, in the case you do not use fabric hoses. When using fabric hoses it might be to tight, so you must open the shells slightly, when you want to pull the cables further through.

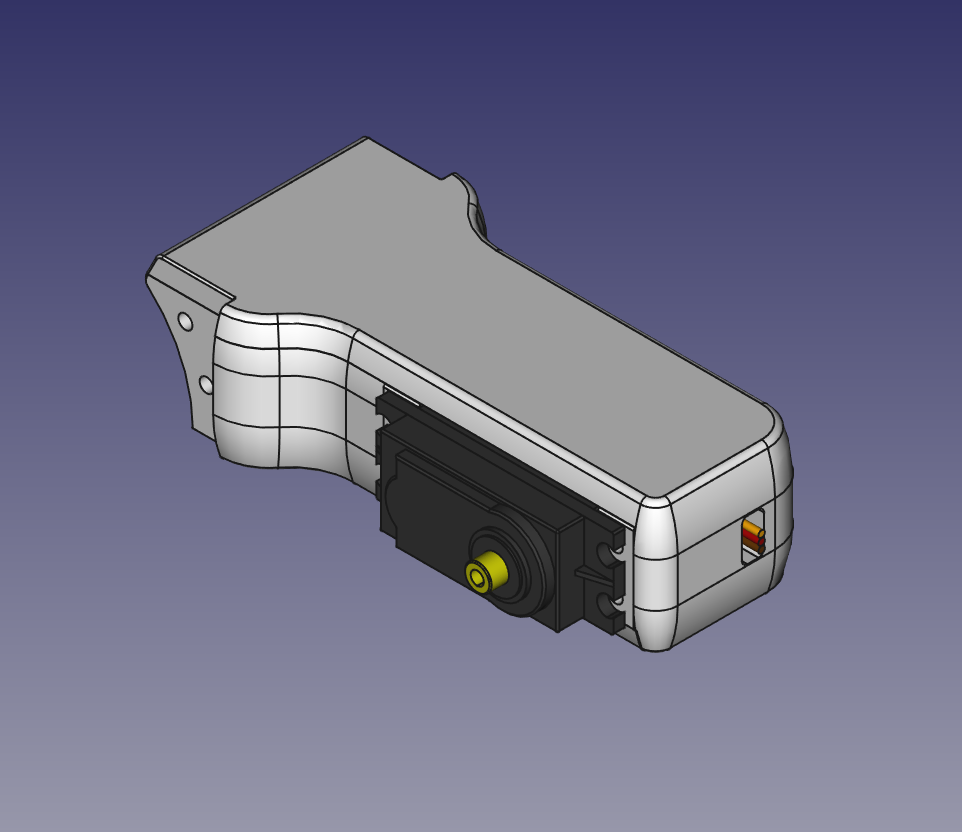
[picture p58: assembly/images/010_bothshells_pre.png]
010 - Both Shells


Use now four M3x20 to screw the servo into place and with it both the top and bottom shell, so they cant come apart without unscrewing them.

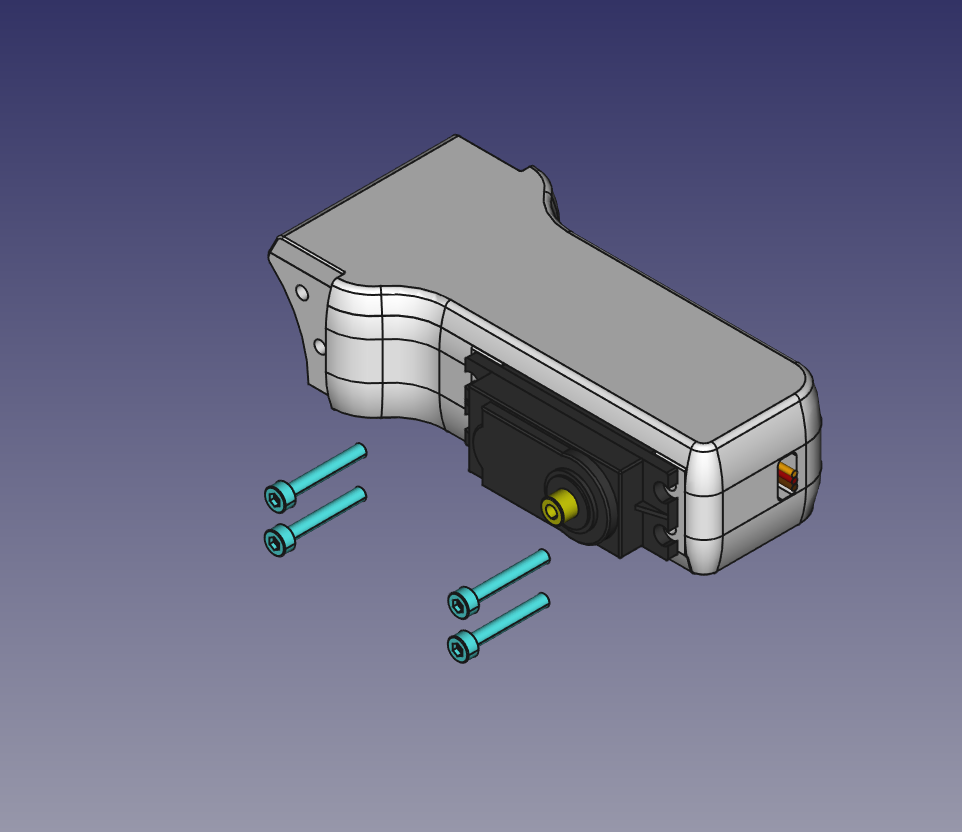
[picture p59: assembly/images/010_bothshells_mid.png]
010 - Both Shells


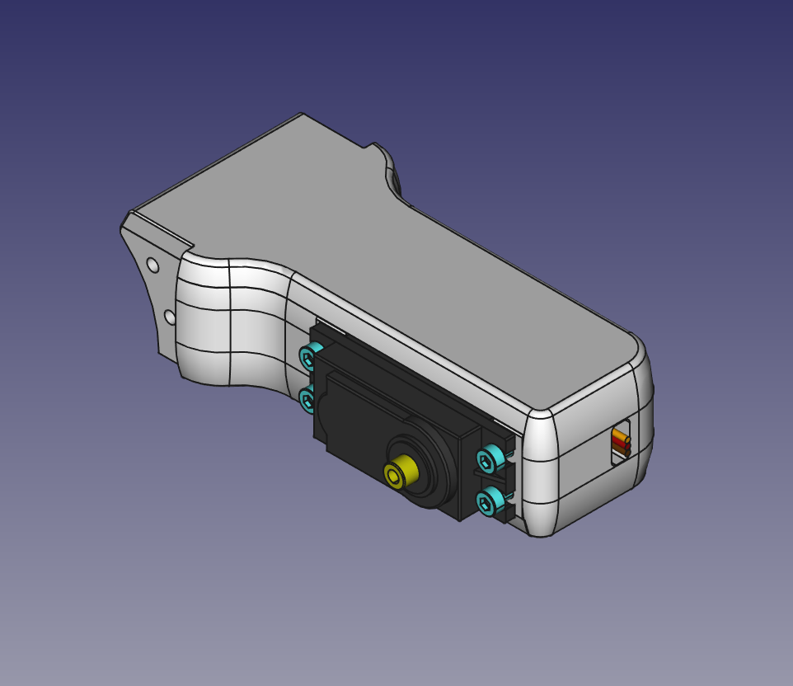
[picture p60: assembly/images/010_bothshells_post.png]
010 - Both Shells


### Complete Upper Leg ###

Now with both shell attached to each other and the servocables of the lower and upper leg routet through, place four M3 nuts in the four rear-facing pockets.

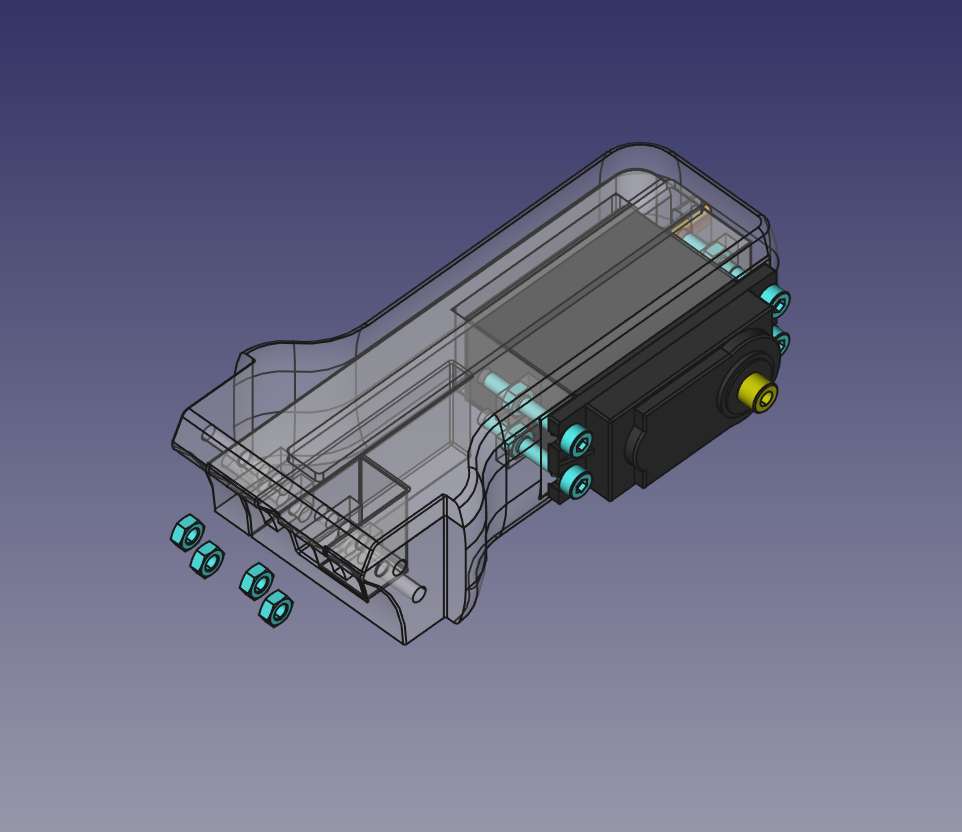
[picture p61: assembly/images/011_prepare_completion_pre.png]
011 - Preparations before completion


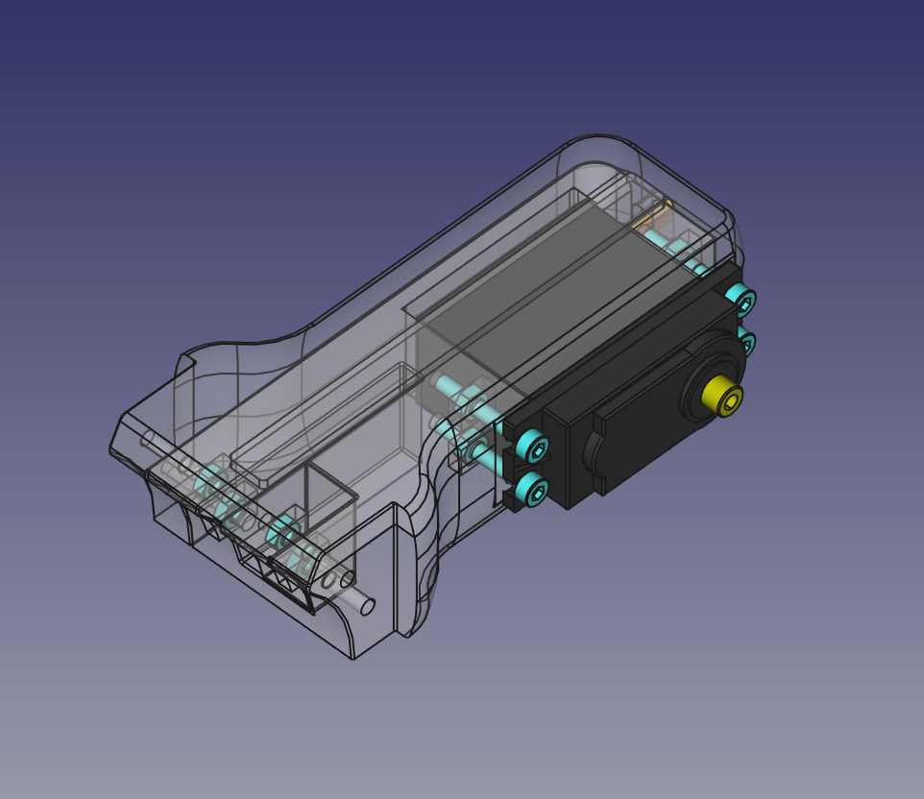
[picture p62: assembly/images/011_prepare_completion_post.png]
011 - Preparations before completion


Place then both shells on the wrist so that the screwholes in the servohorn and ballbearing mounts align with those in the shells. Use four M3x20 screws, to screw everything together to complete the upper leg.

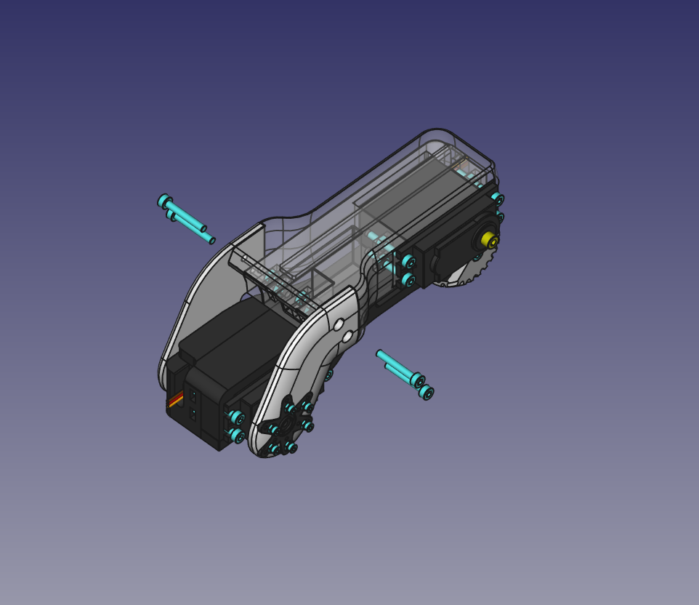
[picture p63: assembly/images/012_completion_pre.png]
012 - Completion of the Upper Leg


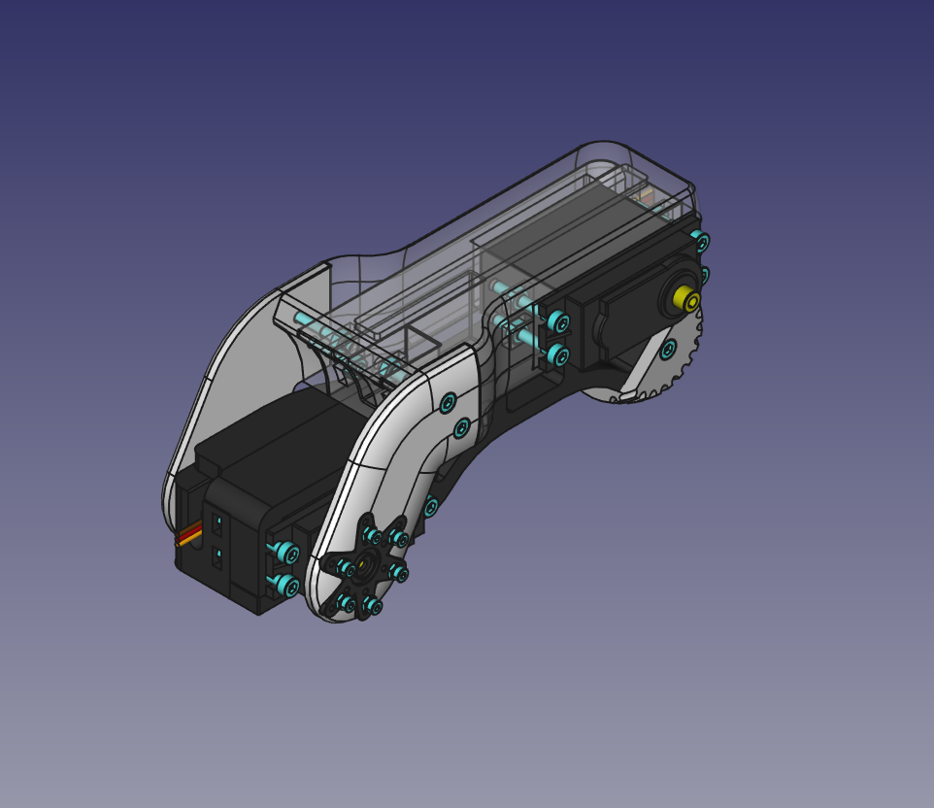
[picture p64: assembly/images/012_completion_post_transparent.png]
012 - Completion of the Upper Leg


This is also the robots legs resting position, which results in the legs laying flat.

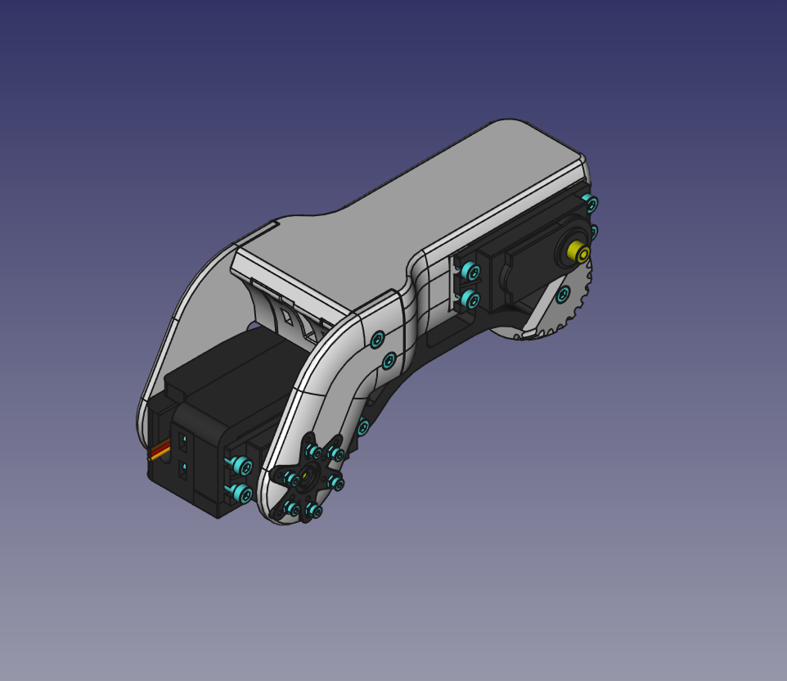
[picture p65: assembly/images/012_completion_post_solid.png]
012 - Completion of the Upper Leg


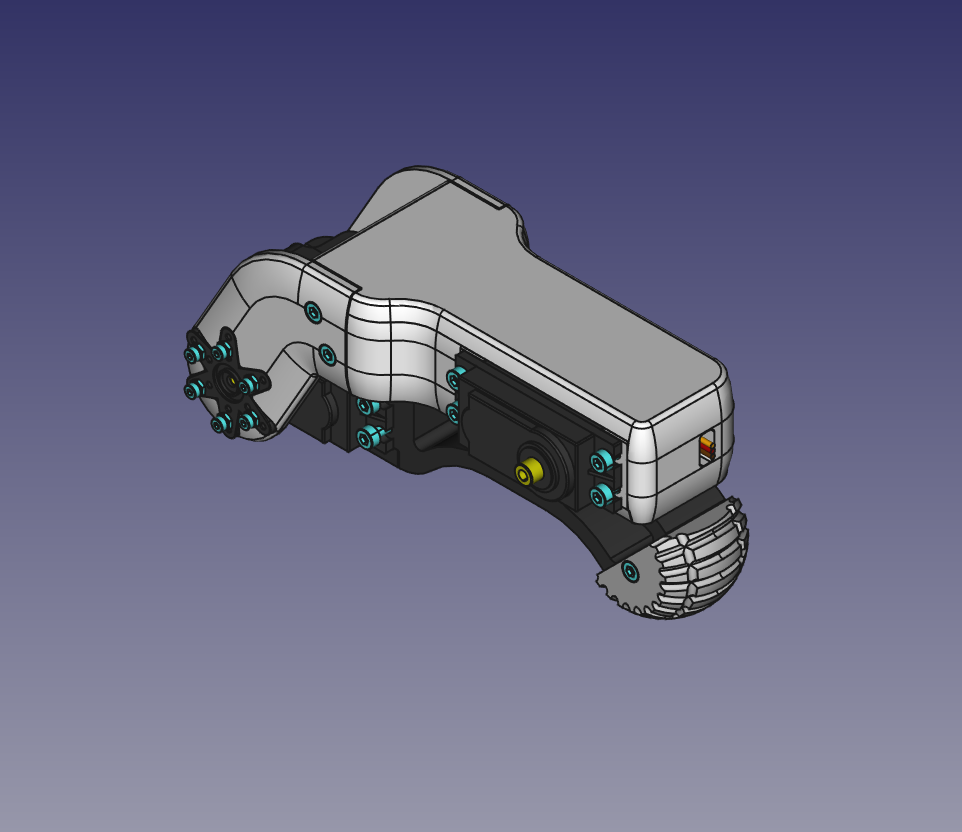
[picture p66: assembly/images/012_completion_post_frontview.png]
012 - Completion of the Upper Leg


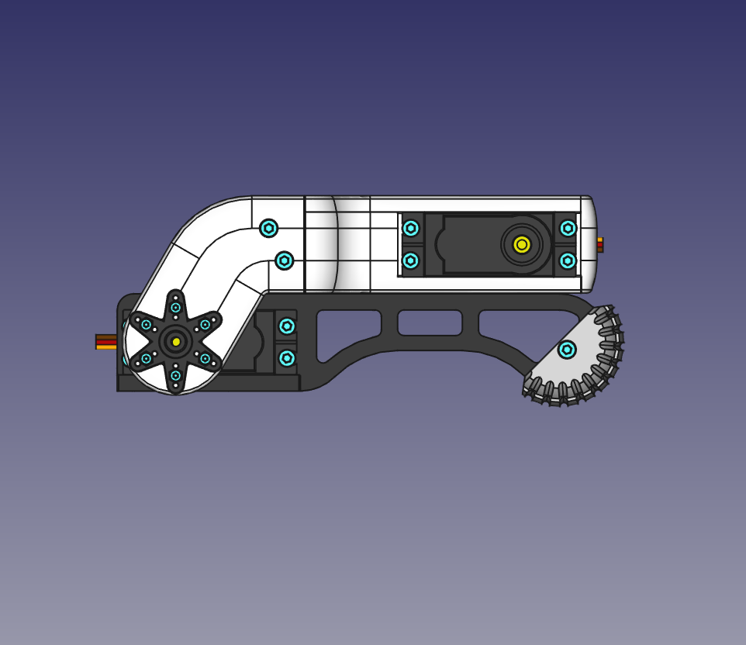
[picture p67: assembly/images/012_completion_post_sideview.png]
012 - Completion of the Upper Leg


For the robots normal standing position the wrists servo is at 90° while the upper legs servo is at 120° or 60°, depending which leg.

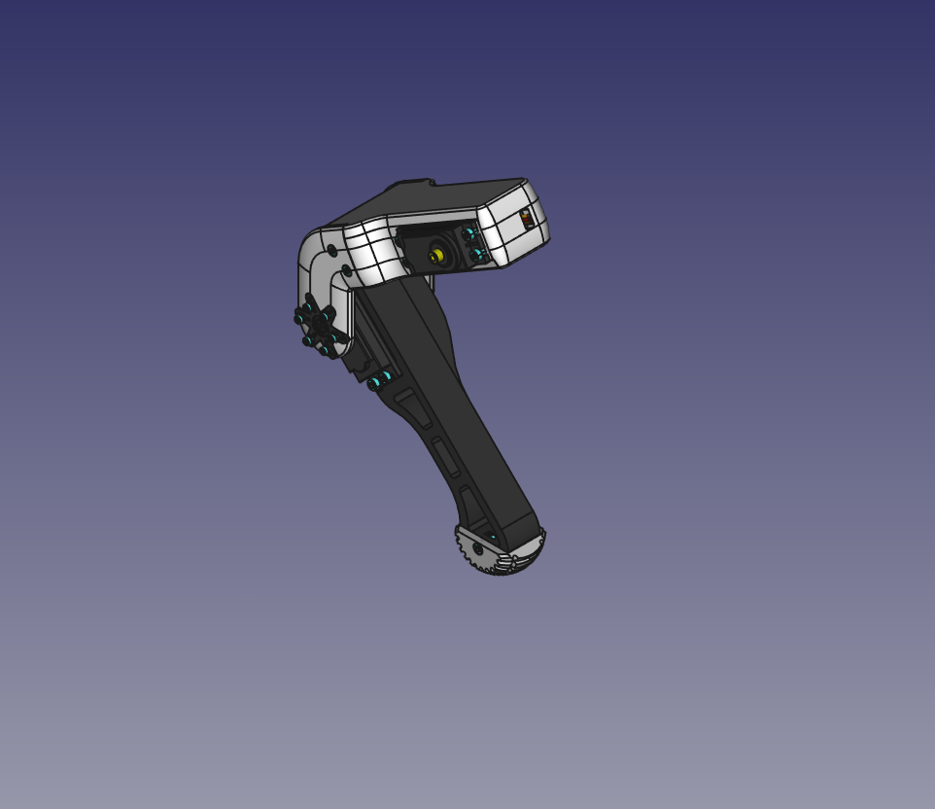
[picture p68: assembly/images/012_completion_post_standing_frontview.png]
012 - Completion of the Upper Leg


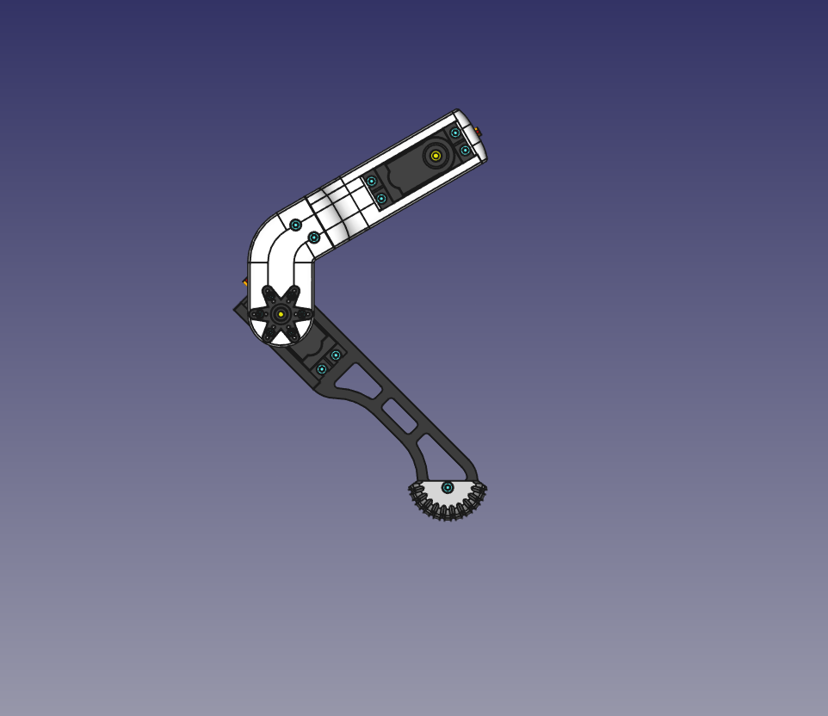
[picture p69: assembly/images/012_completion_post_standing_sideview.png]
012 - Completion of the Upper Leg


## Shoulder Joint ##

You need to make two identical Shoulder Joints for both sides - this means, that you need two mirrored pieces for the Shoulder Joint Servomount. This time instead of mounting both on the right or left, each the left and right side will have one of the mirrored pieces.

### Parts ###

**you might use only two M2x8 on each servohorn cap to screw the servohorn into place and thus reducing the amount of M2x8 screws and M2 nuts by 2/3**

**if you have M2x6 then use these instead of the M2x8 which are only in use, because it was easier to buy the screws and nuts in bulk**

| Total Amount | Part |
|---|---|
|  4x | MG996R at 90° |
| 16x | Servo rubber dampeners (should be shipped with your servo) |
|  4x | FSH6S Servohorn |
|  |  |
|  |  |
|  4x | [Shoulder Joint Servomount](../parts/SpotMicroESP32_parts_v1_0_0/README.md#shoulder-joints) (2x right-handed, 2x left-handed) |
|  4x | [Shoulder Joint Servohorn Cap](../parts/SpotMicroESP32_parts_v1_0_0/README.md#shoulder-joints) |
|  4x | [Shoulder Joint Ball Bearing Pin](../parts/SpotMicroESP32_parts_v1_0_0/README.md#shoulder-joints) |
|  |  |
|  |  |
| 36x | M3 nuts |
| 16x | M3x20 |
| 20x | M3x8 |
| 24x | M2 nuts |
| 24x | M2x8 |

### Servohorn Cap Preparation ###

You need to screw the M2 nuts on the M2x8 first, otherwise it would hinder the mounting of the servohorn. You can't use the bare M2x8 screws without the nuts in this step, because they would stick out from the other side and touch the servo unavoidably, which would result in blocking the servo movement or other damage. **You might consider using M2x6 instead and ditch the need for M2 nuts here completly.** Screw the servohorn into place, using the middle hole on each little arm.

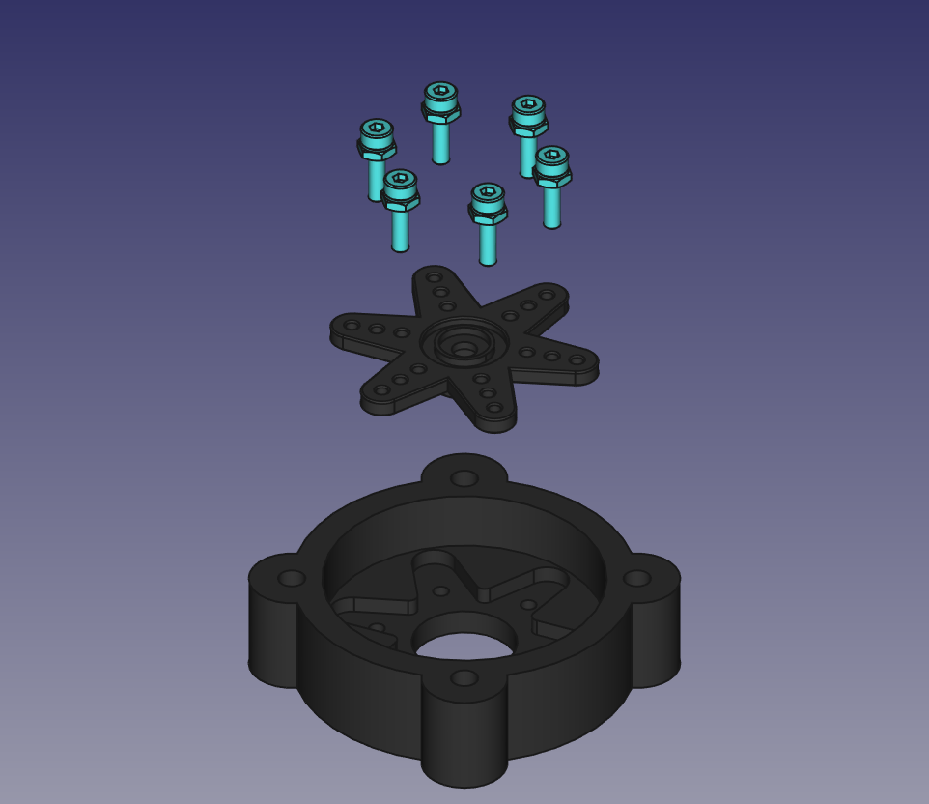
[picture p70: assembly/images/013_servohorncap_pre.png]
013 - Servohorn Cap Preparation


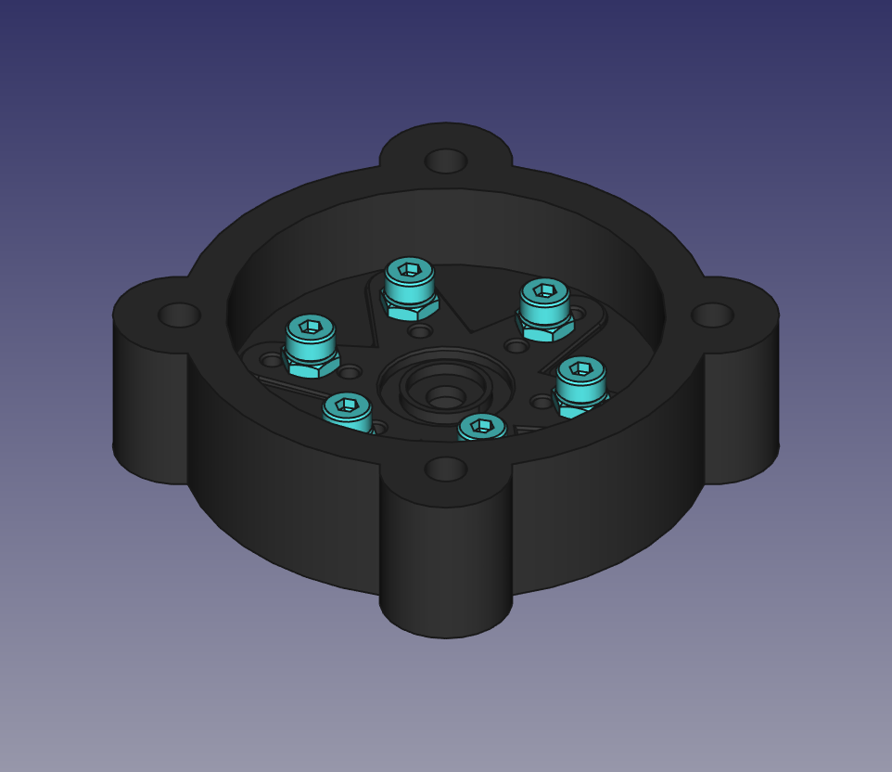
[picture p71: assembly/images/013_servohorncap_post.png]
013 - Servohorn Cap Preparation


### Attach Ballbearing Pin to Servomount ###

Insert 1x M2 nut into the small space in the Shoulderjoint Servomount. Screw 1x M2x8 through the ball bearing pin and attach it to the Shoulderjoint Servomount.

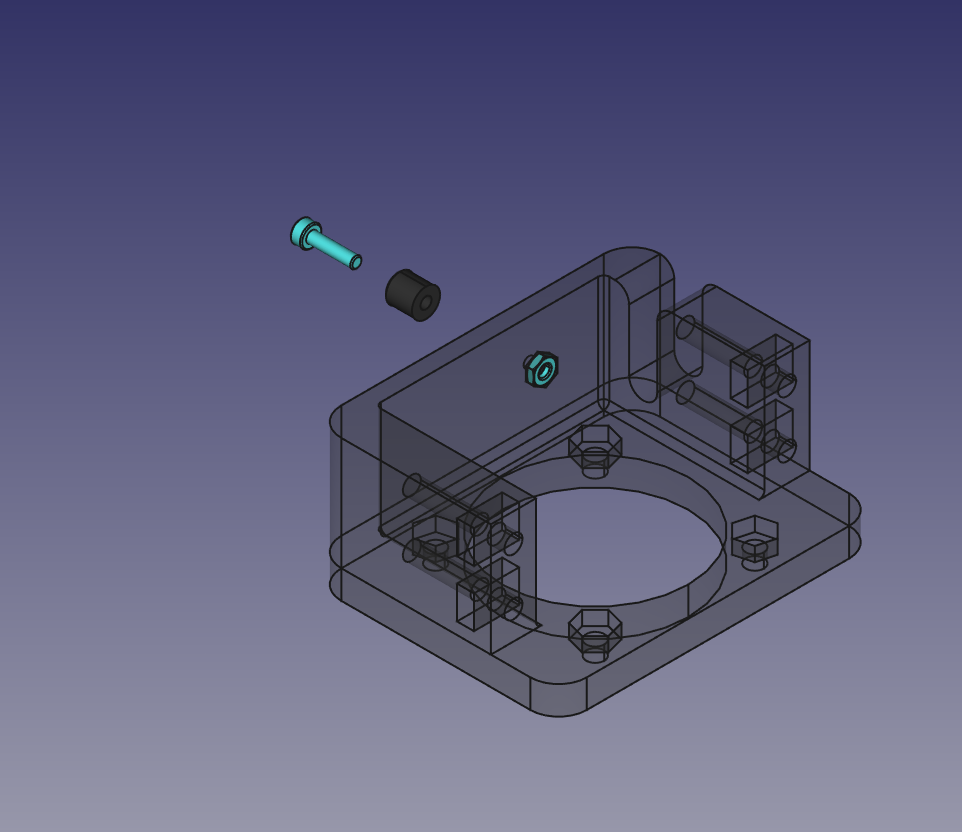
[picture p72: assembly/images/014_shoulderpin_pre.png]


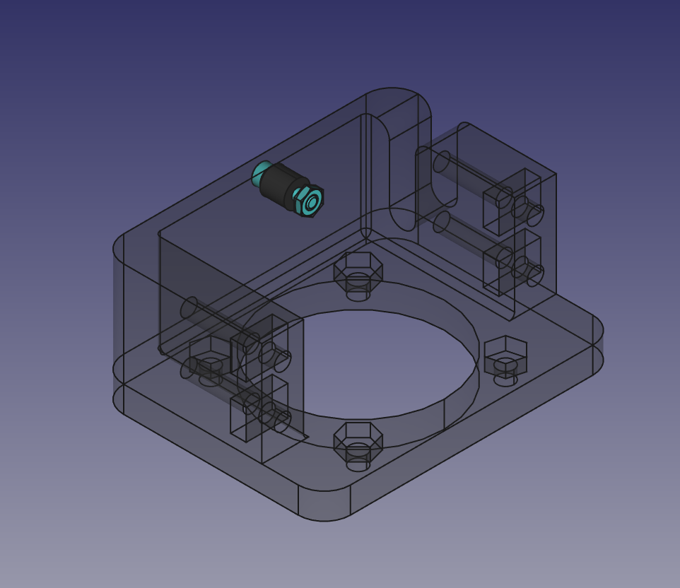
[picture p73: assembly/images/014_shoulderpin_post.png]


### Attach Servohorn Cap to Servomount ###

Now insert 4x M3 nuts into to pockets in the base of the Servomount and screw the Servohorn Cap with 4x M3x8 into place.

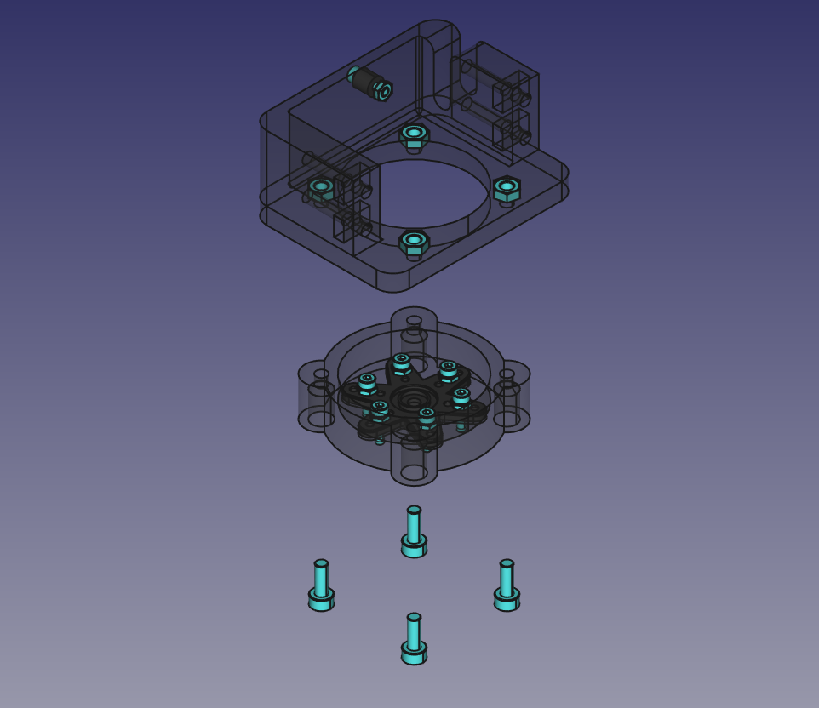
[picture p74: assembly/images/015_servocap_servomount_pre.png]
015 - Attach Servohorn Cap to Servomount


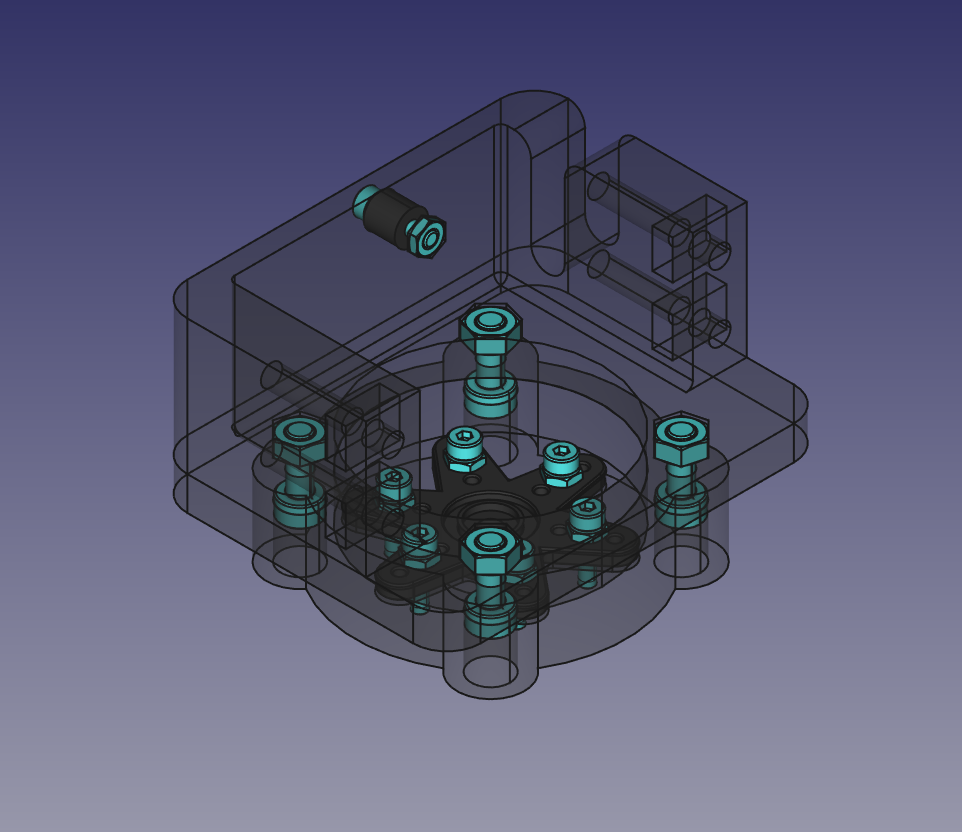
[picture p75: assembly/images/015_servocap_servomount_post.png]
015 - Attach Servohorn Cap to Servomount


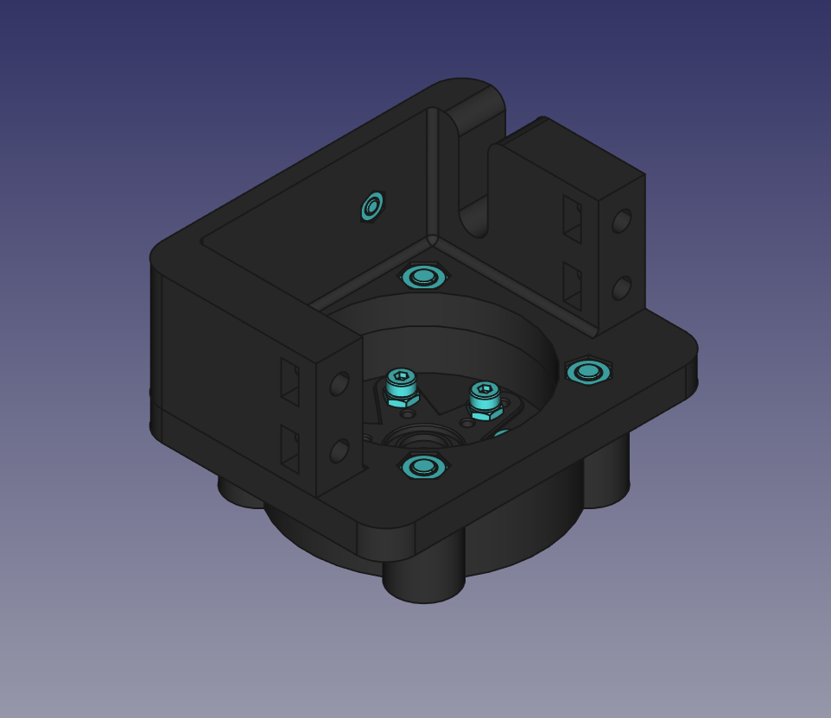
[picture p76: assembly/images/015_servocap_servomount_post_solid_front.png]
015 - Attach Servohorn Cap to Servomount


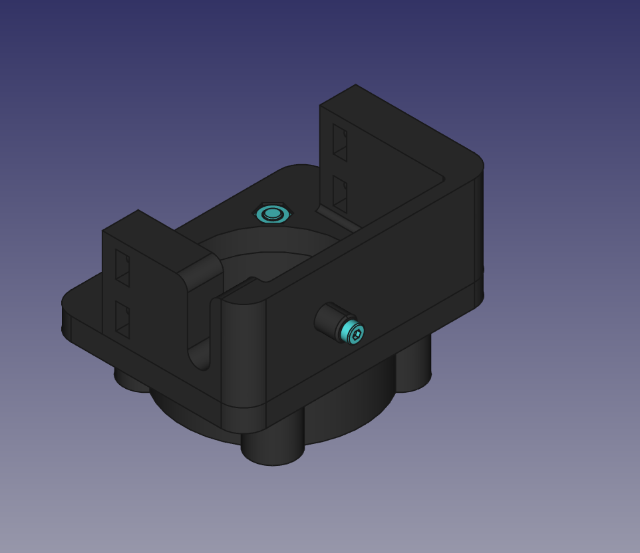
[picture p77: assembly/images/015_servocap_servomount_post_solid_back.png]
015 - Attach Servohorn Cap to Servomount


### Attach Shoulder Joint to upper Leg ###

For the robots normal standing position the wrists servo is at 90° while the upper legs servo is at 120° (left legs) or 60° (right legs), depending which leg. Make sure you have actually positioned your servos correctly before, **otherwise you should do the movement befor assembling further**. When mounting the Shoulder Joint you wont align it to the upper leg along the upper star, but along the first to the right (left legs) resp. first to the left (right legs). Since the servohorn has six arms, each arm means an increase of 60°. For the left legs use this picture as an orientation.

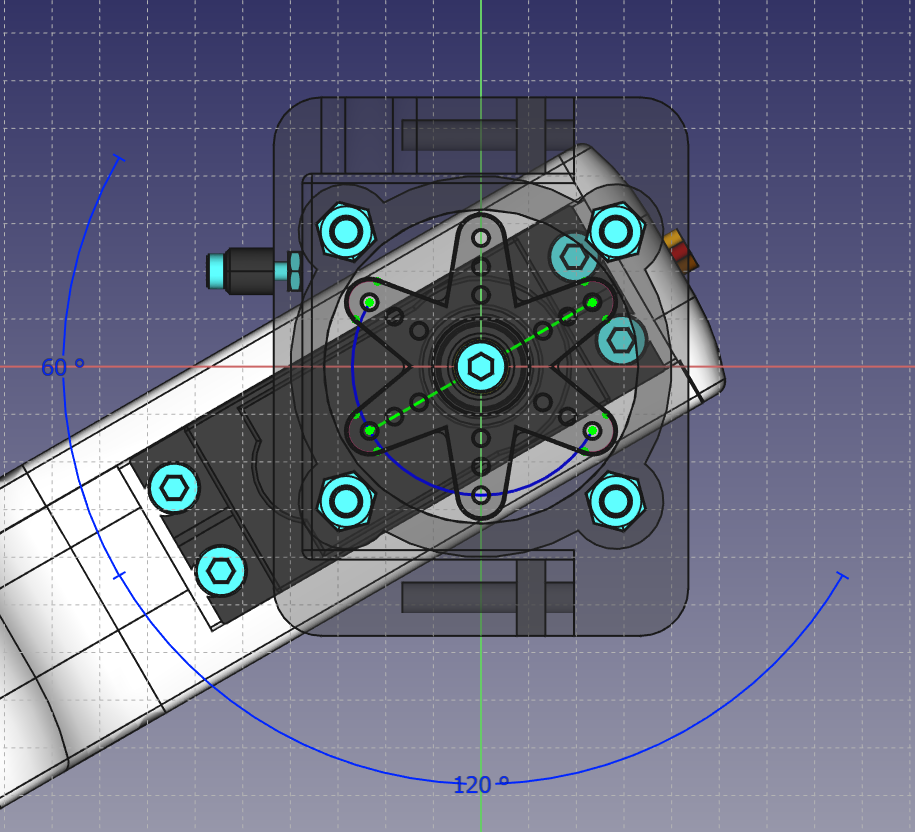
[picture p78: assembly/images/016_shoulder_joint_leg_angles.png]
016 - Attach Shoulder Joint to upper Leg


The assembly is straight forward. Take an M3x8 screw and screw the assembled shoulder joint into place, as mentioned above. It is intentional, that the upper leg wont move between both horizontal endpoints, but instead could retract the leg further to the back than to the front.

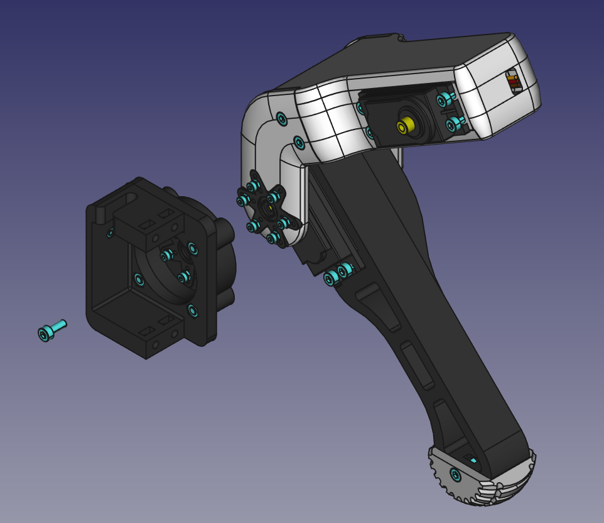
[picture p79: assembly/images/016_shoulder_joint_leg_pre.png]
016 - Attach Shoulder Joint to upper Leg


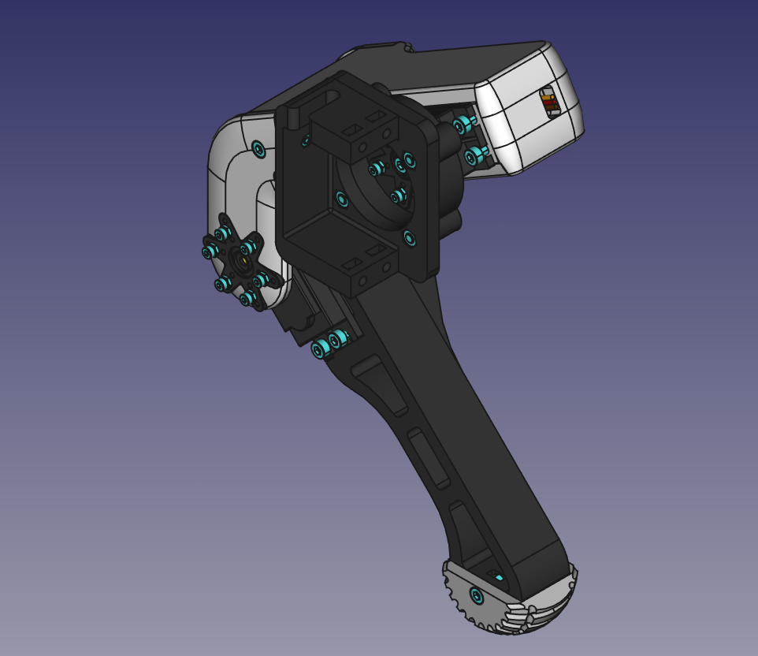
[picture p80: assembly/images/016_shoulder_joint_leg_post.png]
016 - Attach Shoulder Joint to upper Leg


016 - Attach Shoulder Joint to upper Leg

### Attach Servo to Shoulder Joint ###

Make sure the servos you want to place are at 90°. Place 4x M3 nuts into the pockets for mounting the servo. Place the servo now into its pocket and screw it into place with 4x M3x20.

017 - Attach Servo to Shoulder Joint

017 - Attach Servo to Shoulder Joint

017 - Attach Servo to Shoulder Joint

### Shoulder Joint Completed ###

You have now succesfully attached the Shoulder Joint to the upper leg. With this you have now completed the front left leg. Repeat the steps for the other 3 legs and make sure you use the mirrored parts when building the right legs and the left legs. **And keep in mind, that the shoulder joint uses the mirrored parts for the front or rear leg on both sides!**

018 - Shoulder Joint Completed

018 - Shoulder Joint Completed

### Overview of all of the four legs ###

With the front left (FL) leg finished, rebuild the rear left (RL) leg with the same steps. But this time use the mirrored shoulder joint piece instead. The picture below shows both legs, where the only difference is the direction the servo in the shoulder joint is facing. Both gears should face outwards towards the nose or back of the robot.

019 - Overview of all of the four legs

The same applies to the front right (FR) and rear right (RR) leg, with both servo gears facing outwards. Use for the right sided legs also the mirrored copies of the lower and upper leg parts. Keep in mind, that you have set the right angles for your servos prior to assembly, with the servos in the shoulder joint being at 90°, the servos in the upper legs at 60° and the servos in the wrists at 0°.

019 - Overview of all of the four legs

When all of your legs are assembled the should look like this, with the front legs shoulder servos gears facing to the front of the robot and the rear shoulder servos facing backwards.

019 - Overview of all of the four legs

## Connecting to the Shoulders ##

**you might use only two M2x8 on each servohorn cap to screw the servohorn into place and thus reducing the amount of M2x8 screws and M2 nuts by 2/3**

**if you have M2x6 then use these instead of the M2x8 which are only in use, because it was easier to buy the screws and nuts in bulk**

| Total Amount | Part |
|---|---|
|  4x | FSH6S Servohorn |
|  |  |
|  |  |
|  2x | [Outer Shoulder](../parts/SpotMicroESP32_parts_v1_0_0/README.md#chassis)|
|  |  |
|  |  |
|  4x | M3x8 |
| 24x | M2 nuts |
| 24x | M2x8 |

Screw the servohorns to the outer shoulder piece with twelve M2x8 screws and nuts.

020 - Connecting to the Shoulders

020 - Connecting to the Shoulders

### Front & Rear Legs ###

Screw the front legs to the outer shoulder using two M3x8 screws. Make sure the servos in the shoulder joints are at 90° and that the arms of the servohorn are perfectly perpendicular.

020 - Front & Rear Legs

020 - Front & Rear Legs

Repeat this for the rear legs as well, so that both outer shoulder pieces face outwards.

020 - Front & Rear Legs

020 - Front & Rear Legs

The front and rear legs with the shoulder should look like this.

020 - Front & Rear Legs

## Body ##

| Total Amount | Part |
|---|---|
|  4x | 625zz ball bearings without flange |
|  |  |
|  |  |
|  2x | [Inner Shoulder](../parts/SpotMicroESP32_parts_v1_0_0/README.md#chassis) |
|  2x | [Top Shoulder](../parts/SpotMicroESP32_parts_v1_0_0/README.md#chassis) |
|  2x | [Bottom Shoulder](../parts/SpotMicroESP32_parts_v1_0_0/README.md#chassis) |
|  2x | [Chassis Side](../parts/SpotMicroESP32_parts_v1_0_0/README.md#chassis) |
|  1x | [Circuitry Mountingplate](../parts/SpotMicroESP32_parts_v1_0_0/README.md#chassis) **(choose either the XL4016 or SZBK07 type, depending on your chosen larger buck-converter)** |
|  |  |
|  |  |
| 24x | M3 nuts |
| 24x | M3x8 |

### Inner Shoulders ###

Add into each the top and bottom shoulder block two M3 nuts. Make sure you have oriented the blocks the right way, so that the pockets for the nuts that will be used to hold the covers are facing into the body.

021 - Inner Shoulders

Screw the inner shoulder with four M3x8 screws into place, so that the screwsheads will sink into their pockets.

021 - Inner Shoulders

021 - Inner Shoulders

### Chassis ###

Take the chassis side piece and place four M3 nuts into their pockets - the flat side should face outwards and the long cutout for the circuitry mountingplate should be at the bottom. **Chose the mountingplate corresponding to your bigger buck converter - the XL4016 or SZBK07** https://github.com/michaelkubina/SpotMicroESP32/tree/master/electronics

021 - Chassis

Put your ***(pre-populated ???)*** circuitry mountingplate between both sides.

021 - Chassis

021 - Chassis

Now attach both inner shoulders to it with each four M3x8 screws and the bigger blocks being at the top.

021 - Chassis

The assembled chassis should look like this.

021 - Chassis

### Mount legs to chassis ###

Attach now the ball bearings to your shoulder joints. Put into the front of the top and bottom shoulder block M3 nuts. Screw the front legs assembly to the shoulder block with four M3x8 screws.

022 - Mount legs to chassis

022 - Mount legs to chassis

Repeat the steps for the rear legs as well.

022 - Mount legs to chassis

022 - Mount legs to chassis

When finished, your SpotMicroESP32 should look like this.

022 - Mount legs to chassis

## Head with ESP32-CAM ##

| Total Amount | Part |
|---|---|
|  1x | ESP32-CAM with OV2640 (Version 2! with slightly longer cable) |
|  2x | HC-SR04 Ultrasonic Sensor |
|  |  |
|  |  |
|  1x | [Front Cover Optimized](../parts/SpotMicroESP32_parts_v1_0_0/README.md#hull) |
|  1x | [Sensormount for the ESP32-CAM](../parts/SpotMicroESP32_parts_v1_0_0/README.md#hull) |
|  1x | [Cameramount for the ESP32-CAM](../parts/SpotMicroESP32_parts_v1_0_0/README.md#hull) |
|  1x | [Cameramount Counterpiece for the ESP32-CAM](../parts/SpotMicroESP32_parts_v1_0_0/README.md#hull) |
|  |  |
|  |  |
|  4x | M3 nuts |
|  6x | M3x8 |

Place the ESP32-CAM into the designated place of the Cameramount. Screw the counterpiece with two M3x8 screws into place, with the small pads facing towards the ESP32-CAM thus preventing the PCB from lifting. Place now the two HC-SR04 into their spaces in the sensormount-piece, but dont push them all way down yet. Instead leave some half centimeter space.. Push now the Cameramount-piece on top of if, so that the wedges slide on top of the HC-SR04 PCBs, thus preventing them from slipping back out again. It might be necessare to hone down a small portion of the lower ends of the wedges.

Place now four M3 nuts into the spaces in the front cover, push the sensor- & cameramount into place and screw all of it with four M3x8 screws into place. The head is now assembled.

## Head with OV7670 (DEPRECATED) ##

| Total Amount | Part |
|---|---|
|  1x | OV7670 VGA Camera w/o FIFO |
|  2x | HC-SR04 Ultrasonic Sensor |
|  6x | 5mm LED (White) |
|  |  |
|  |  |
|  1x | Front Cover |
|  1x | Sensormount |
|  1x | Cameramount |
|  |  |
|  |  |
|  8x | M3 nuts |
|  8x | M3x8 |

### Cameramount ###

Place four M3 nuts into the pockets below the tilted camera-base.

023 - Cameramount

023 - Cameramount

Screw your OV7670 VGA Camera into place with four M3x8 screws.

023 - Cameramount

023 - Cameramount

### Sensormount ###

**You will need to bend (or solder) the pins of the HC-SR04 in a fashian that they are parallell to the PCB and facing inwards. If the pins are perpendicular to the PCB you would not have enough space, to attach the head to the body. If being parallel and facing outwards, you would not be able to do the assembly at all. If you feel more comfortable with soldering the cables directly to the PCB, do this instead.**

Place your six 5mm LED (white) into the six small holes of the sensormount with their pins in the orientation as seen in the image. The two white LEDs in the middle row (highlighted in pink or green) need to be rotated by 90°, otherwise you would not be able to assemble proberly.

023 - Sensormount

023 - Sensormount

Place now both HC-SR04 Ultrasonic Sensors into the sensormount, but dont push them into their pockets completly yet - leave them about half a centimeter of space for now. Make sure you have oriented them the right way, so that the internal oscillator fits into the small pocket at the sides of the sensormount. Place the assembled cameramount on top of it and push both pieces together. Make sure you route the pins of the LEDs through their holes at the top and bottom row, and the pins in the middle row along the camera-base near the HC-SR04's.

023 - Sensormount

When your Cameramount slides over the HC-SR04 Ultrasonic Sensors (still sticking out ca. half a centimeter), push the cameramount and the sensors gently down. 

023 - Sensormount

The Cameramount has two small wegdes (highlighted green) on the sides of the camera-base, which prevent the HC-SR04 from sliding out of their pockets. When pushing both the sensormount and the cameramount together, those wedges should push both HC-SR04 down. 

023 - Sensormount

### Build Assembly into front Cover ###

Place four M3 nuts into the spaces in the front cover.

023 - Build Assembly into front Cover

Place the whole assembly into the front cover and screw it with four M3x8 into place.

023 - Build Assembly into front Cover

Your finished head-unit should look like this.

023 - Build Assembly into front Cover

023 - Build Assembly into front Cover

## Tail ##

The following section needs to be redone as the referenced piece is currently deprecated 😅

| Total Amount | Part |
|---|---|
|  1x | 1,8" TFT with ST7735 with SD-Card  |
|  1x | Push Button (latching, **not momentary**) |
|  |  |
|  |  |
|  1x | [Rear Cover Shell Longer Version](../parts/SpotMicroESP32_parts_v1_0_0/README.md#hull)|
|  |  |
|  |  |
|  4x | M3 Nuts |
|  4x | M3x8 |

### Mount TFT Screen and Pushbutton ###

Place the 1,8" TFT with SD-Card into its designated pocket and screw it with four M3x8 screws into place - counter it with four M3 nuts from behind.

024 - Mount TFT Screen and Pushbutton

Remove the nut from your pushbutton and slide it through the hole - counter it with the nut again from behind.

024 - Mount TFT Screen and Pushbutton

024 - Mount TFT Screen and Pushbutton

Your rear cover is complete.

024 - Mount TFT Screen and Pushbutton

## Top and bottom Cover ##

| Total Amount | Part |
|---|---|
|  1x | [Bottom Cover Split Front](../parts/SpotMicroESP32_parts_v1_0_0/README.md#hull) **do not use yet! See note above!** |
|  1x | [Bottom Cover Split Rear](../parts/SpotMicroESP32_parts_v1_0_0/README.md#hull) **do not use yet! See note above!** |
|  1x | [Top Cover Split Front](../parts/SpotMicroESP32_parts_v1_0_0/README.md#hull)  |
|  1x | [Top Cover Split Rear with OLED](../parts/SpotMicroESP32_parts_v1_0_0/README.md#hull)  |
|  |  |
|  |  |
|  8x | M3 Nuts |
|  8x | M3x8 |

## Connect both cover halves ##

Take the front and rear half of the top cover. Use four M3x8 screws to screw both pieces together - counter them with four M3 nuts.

025 - Connect both cover halves

025 - Connect both cover halves

Repeat this for the bottom cover halves as well.

025 - Connect both cover halves

## Mount covers ##

| Total Amount | Part |
|---|---|
| 16x | M3 nuts |
| 16x | M3x8 |

In order to mount the head-unit, the tail and the top and bottom cover to the body, you need to add the M3 nuts into the top and bottom blocks in the front and rear shoulders (highlighed green).

026 - Mount Head

026 - Mount Head

### Mount Head ###

Slide the assembled head-unit onto the front shoulder-plate.

026 - Mount Head

Screw it from the top and from the bottom with four M3x8 screws into place.

026 - Mount Head

026 - Mount Head

### Mount Tail ###

Slide the tail onto the body as well and screw it with four M3x8 nuts into place.

026 - Mount Tail

### Mount top and bottom covers ###

Place the bottom cover beneath the body and screw it with four M3x8 into place.

026 - Mount top and bottom covers

Place the top cover over the body and screw it with four M3x8 screws into place.

026 - Mount top and bottom covers

## Assembly Finished! ##

Congratulations, you have now succesfully assembled your SpotMicroESP32.

027 - Assembly Finished!

# what's left? #

**The mountingplate for the circuitry is still missing and is currently being designed!**
Once it's ready i will add the steps necessary as a separate sections in the chassis part.
The mountingplate suits specifically this build. You might use different hardware as i did, and as of this need modifications. Please use the updated Template, once its all finished.

Furthermore i want to adress some shortcomings in this guide. I want to replace all images, where the rubber dampeners are missing (mea culpa) and i want to make it more clear, which servo has to be at which angle for assembly. I realize, that the description are sometimes not very clear...i will need to think of a way to clarify this.

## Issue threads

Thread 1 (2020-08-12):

Short & Long version

Nivek92, 2020-08-12:
Hey Michael,
first I want to say thank you for this great remix of the original MicroSpot. It's actually the first bigger project I want to replicate.

Looking through the parts folder I saw that there is a short and long version for "Limb_Ball_Bearing_Mount" and "Limb_Servohorn_Mount". Which one is the correct one / which one should I use?

Besides that is there anything I can help you with in regards to this project?

michaelkubina, 2020-08-12:
Hello Nivek,

i really appreciate that you like my remix! I am glad you ask, because this was the only part that i made in 5 different versions, of which only two made it in this repo.

You should use the "long version", which will result in the legs being fully bend when the robot is in its resting position. The upper and lower leg will be parallel in the end (=).

The "normal version" copies the dimensions of the original design, which results in the legs not being able to fully collapse. This means the legs will always look like an angle brackets in the end (<). Maybe with some force you could damage some parts as well, because theoretically you would be able to "overbend" the joint.

Right now i can't think of anything you could help with specifically. I am working an the assembly guide, and will hopefully soon start designing the mountingplate for all of the electronics. Maybe, when assembling one of your self, you could post your issues, or ideas for improvements and so on here in this bugtracker. I guess this would help...

...will you write about the progress anywhere? Blog, Youtube, Reddit or so? This would be interesting, because i could learn something in return.

Nivek92, 2020-08-13:
Thanks for the quick answer, I had nothing in particular in mind, just wanted to offer a helping hand.

I certainly make sure to share any issues and ideas with you.

In regards to the programming I want to look at https://spotmicroai.readthedocs.io/en/latest/ first and then decide if I want to implement everything myself and build on that library.

But either way I make sure to document the build process and the programming and share it with you but I still have to decide where to document it. Will let you know as soon as I decided.

michaelkubina, 2020-08-26:
The distinction between long and normal version is now in the 3d printed partlist as an additional note. Furthermore it is mentioned in the assembly guide to go with the long version.

Closed 2020-08-26.

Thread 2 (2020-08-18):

Full assembly file pls

yuhao1118, 2020-08-18:
Hi,
Appreciate your hard work! As you have not finish the assembly guide, can I have the full assembly cad file so that I can continue to work on it?

michaelkubina, 2020-08-18:
Hello yuhao,
thank you very much! And thank you for your offer to help, but its something i would like to finish by myself right now, because i am already all into it. I am still working on the assembly guide - its not abandoned ;-) And actually I released it only 8 days ago (which was also the day i started writing it), with the latest addition being made only two days ago. While writing the assembly guide i also build the CAD of an assembled robot - so i have nothing to share here right now for you. But as soon as the CAD-File is complete, i will share it as well, this is for sure.

so i have to aks for a little patience, the next updates will come soon...

I will keep this issue open, as a reminder for releasing the CAD-file

michaelkubina, 2020-08-30:
Hello,

i have completed the assembly guide for all the 3d printed parts. The assembly of the circuitry is not part of it (yet), because this is still in the planning. I added also the FreeCAD-File of the whole robot, which is as complete as it could be right now, but also very messy, because it was build rather quick and dirty as a blueprint for the images needed for this guide. To tidy it up is not a priority for now, because the usecase for this file is rather tight. But who knows, what other will come up with...

I will close this ticket for now, since the guide is completed and the file released.

Closed 2020-08-30.

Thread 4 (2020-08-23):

Servocables rubbing/grinding when routet into the body

michaelkubina, 2020-08-23:
The way the servocables are routed into the body causes them to rub/grind between the edges of the shoulder joint and shoulder top block.

Either or both parts should be modified to prevent damage to the servocables.

michaelkubina, 2020-12-06:
Updated shoulder blocks to mimick original design with smooth roundings, thus at this point preventing grinding. Prototype of Shoulder-Joint-Servomount with routing-holes prototype also in work.

michaelkubina, 2020-12-09:
Shoulder-Joint-Servomount updated with pockets for cable-routing of the lower and upper leg servos

Closed 2020-12-09.

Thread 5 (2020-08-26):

Covers orientation for printing

Nivek92, 2020-08-26:
Quick question:
Printing the covers, do you print them standing upwards (as they are when you open the file) or do you print them lying down (a big surface makes contact with the printing bed)?

michaelkubina, 2020-08-26:
Hello Nivek,

I printed them standing upwards as in the files. All files should be in their printing orientation, as seen in the screenshots as well.

Because of the surface area being small this way I have used a brim for these and would suggest you do the same. Removing the brim afterwards  is no work at all ;-)

Closed 2020-08-26.

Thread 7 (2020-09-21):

ESP32 Vs Raspberry Pi Zero

Annihil8ted, 2020-09-21:
Hello! I've been following your project pretty closely and I wanted to start off and say thank you/you've done an amazing job! I've got the entire chassis printed and assembled and have just the electronic plate left.

I noticed that you recently posted a preliminary outline of how you plan to place your electronics. I was wondering if I could make a small request and ask if you can also provide a model where a raspberry pi  zero is used instead?

Maybe this deserves another post but I was wondering why the ESP32 over Rpi Zero W? I get that overall, it's microcontroller vs full blown OS but it seems to me that RPI would provide a path for more advance features later down the road?

Is there anything else that you might need assistance on? I'm a software engineer and have a 3D printer on hand to help development and test if needed.

michaelkubina, 2020-09-21:
I am happy that there are already some peoply actually printing my design - this is so cool :-) Do you share your progresses anywhere public?

I am not sure if you are familiar with FreeCAD, because if so you could mod it by yourself so it would work with a Raspi Zero and suit your needs - i have provided the design-files as well. I am not sure if the making of a derivate with the screwholes placed specifically for a RaspiZero would be enough to mount the raspi nicely. The way it is powered and flashed needs to be considered as well, because when using usb-cables internally, the placement of the whole pcb must be with this in mind. There is not much space and i already had to leave spots blank and rearrange everything multiple times for the ESP32 already.

The Raspi Zero has the power-in and data-in in bad spots, which could likely lead to the cable getting pressed against the PCA9685-PWM-Board or LM2596 Buck-Converter. **I cant guarantee** any of this will work, but i have added a "mods" folder within the parts folder. There you will find an **EXPERIMENTAL**-Version for the raspi zero. You will need 3x M2.5x8 screws. The taller pins next to it are for the TTL-Adapter of the ESP32-CAM...if you dont need these, then simply delete the last operation in the FreeCAD-File and export a new STL.
**If you want to print this, than do it all at your own risk! It might be a waste of PLA, i cant tell...but i really hope it is what you requested and that it work like you expected it.**

To answer your question why the ESP32 and not something else? It just because i had it here already and played around with it. There is no real reason, but its cheap, has a lot of features and i already had the enviroment set up for it. But there is a lot of variant of it as well, which makes buying it a bit messy. And actually, as you said, it's more of a microcontroller than a microcomputer.

I will close this ticket and i hope a was able to give you what you wished. If not, then consider it a blueprint for modding...supporting this as well would bind to much of my time ;-)

Closed 2020-09-21.

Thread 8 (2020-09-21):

Larger holes/ deeper channels for sheathed servo wires in upper leg

Annihil8ted, 2020-09-21:
I sheathed my servo cables using a braided nylon sheath however I was unable to snake them through the servo cable hole in the upper leg. I ended up having to use a router to enlarge the hole and snake them through. The next issue then became the channel, particularly the area right there the servo sides, is super tight and causes some binding.

michaelkubina, 2020-09-21:
Thank you for mentioning this, i will certainly adress this! Also I am actually already aware of this issue and have it on my todo list in the projects section of the 3d-printed-parts. I have encountered it too, while assembling my spotmicro using fabric-hoses around the servocables and did not think about it in the design process. I will keep this issue open as a reminder, but right now my priority is to make a documentation on the wiring/circuitry, because i think this is more urgent due to the lack of it.

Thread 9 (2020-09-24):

ST7735 Unable to Source

Annihil8ted, 2020-09-24:
Hello!

I have on hand a display board:

https://www.amazon.com/Display-Module-ST7735-128x160-STM32/dp/B07BFV69DZ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

I was unable to find one with out an SD card and unfortunately  this doesn't drop into the existing slot on the chassis shell tail. It's about 2-3mm too short. Is the side facing center or the side closest to the push button was extended about 2-3mm (including mounting holes, this would be able to fit in.

Alternatively, could you specify a link on where to find a ST7735 that's exactly 1.77 and without SD card? Or even better, the one that you have?

I should also add I'm located in the US.

Thanks!

michaelkubina, 2020-09-25:
This looks like the one i have: https://www.amazon.com/-/de/dp/B082HTWZR6/ref=sr_1_11?dchild=1&keywords=1.77+tft&qid=1601068721&sr=8-11

But you are right, that it's easier to get those with an sd-card-slot than those without. I bought this specific one just because i had it laying around and i read an article about it a long time ago, which lead to buy it: https://www.hackster.io/ocnarf/cheap-1-77-inch-tft-screen-on-esp32-ebe208

I think i will change the part, to fit the one you mentioned (i already ordered one 1.8" TFT with SD-Card today for myself, should be delivered by tomorrow), mainly because it would be easier for others to buy and it costs the same as the one without an sd-card + plus you could try to utilize the sd-card, if you like to.

I keep this issue open, till i changed the part - afterwards there will be two versions of the tail. Also it should remid me, to clarify that those small cheap tft's have different distances of their mounting holes...

...i guess this the point where modding starts ;-)

michaelkubina, 2020-09-27:
I made now some adjustments to the longer rear-cover to fit the 1.8" TFT. Will print the mounting-plate (cutout) tomorrow evening i think, to test if the display fits and if there are any issues. If everything works out like i hope i would upload the files afterwards.

Annihil8ted, 2020-09-28:
Awesome, excited to see the mods! Thanks for being so responsive too!

michaelkubina, 2020-09-28:
The print was successfull, had to make just a little adjustment afterwards. You can either test beforehand if your display could be mounted properly with the STL i attached (just a cutout ouf the mounting-place)...or you can use directly the full new rear-cover-piece from the parts-directory.

I also made this display the new default-display for this build.

[1_8_tft_mounting_test.zip](https://github.com/michaelkubina/SpotMicroESP32/files/5294774/1_8_tft_mounting_test.zip)

I close this ticket within the next couple days or after hearing how it went for you - depending what comes first ;-)

Annihil8ted, 2020-09-29:
I'm printing it right now and will let you know how it fits!

Annihil8ted, 2020-09-30:
I printed the long 1.8 ftf rear cover and my tft screen fits perfectly!

Annihil8ted, 2020-09-30:
I will say however in it's current placement, the SD card cannot be used as it'll hit the walls.

michaelkubina, 2020-09-30:
> I'm not sure how you would be able to place the TFT screen such that the SD is made accessible while not in an awkward placement for the screen.

This was something i thought about as well...we might add a slot so one could use a SD-Card, which would stick out at the bottom about 5-10mm in the current state. Or moving the display a little, which might then look misplaced.

If we want to use an SD-Card as some kind of memory, we can always use the micro-sd slot of the ESP32-CAM - at least i think so. You just would not be able to remove it easily...

Annihil8ted, 2020-09-30:
I would opt for the slot because 1) It's pretty well concealed and 2) It makes swapping cards super simple. Then again that's if you deem it even worthy to invest the time to go back in and modify the stl.

I'm also in a little different boat than you too; I plan on using a raspberry pi which has storage up to whatever card you place in it. I'm not sure if the regular ESP32 has storage

michaelkubina, 2020-10-01:
The ESP32 has 512KB SRAM I think and 4MB memory for flashing. Would need to look it up again, but it not this important now.

I will reopen this issue and modify the file - not immediately but soon. I guess having the option to use the slot/sd-card or not is worth the effort, as long as other can benefit from the mod.

michaelkubina, 2020-10-12:
I have made a slot/hole for the sd-card and moved the screen-pocket and the hole for the pushbutton some tiny amount. It prints good, but your printer should be able to brigde 2cm properly. It does not look weird or anything...it might be fiddly to remove the sd-card/pushing it in...but when you use an sd-card-to-micro-sd-adapter you can just remove the micro-sd-card very nicely and leave the rest in place.

I will close this isse, as the parts are now updated and working properly.

Closed 2020-10-12.

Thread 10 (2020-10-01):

why not have  right leg stl file??

domfdk13, 2020-10-01:
I don't have the right leg of the spot micro with esp 32 added and stl files of limb top shell and limb bottom shell thumbnails.  No matter how much I look for, please add the file to github.

michaelkubina, 2020-10-01:
Hi, there are no files for the right legs and there wont be, because you can simply mirror the necessary pieces in you slicer-software. Mirror along the x or y axis...it doesn't matter, because there is no difference which axis you chose, as the resulting piece is the same.

In the parts list is a detailed description which parts need to be mirrored for your build - actually nearly all parts from the legs, except the foot-tips, shoulderjoint servorhorn-cap and  the ball-bearing-pins. Dont forget to print those twice.

I wont add right-hand-sided pieces to those already published, because this would mean to replace all the mirrored pieces, if i make some changes to those parts. Apart from being more work for me it could also lead to parts being different, because i forgot to update them. So with just mirroring the pieces, it is the safest way for all...

Closed 2020-10-01.

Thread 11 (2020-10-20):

Revising nutholes in lower and upper leg

michaelkubina, 2020-10-20:
While assembling lower and upper leg, the nuts have to much play, which leads to misalignments and causes problems during asembly. Changing the size/depth of the pockets or adding thin walls might be a solution

Annihil8ted, 2020-10-27:
I too have found some trouble when assembling. I had to jam a small flat head driver to prevent the nut from spinning. Sometimes the nut would also go too deep. Not a big problem but some headaches when assembling

brukhabtu, 2023-08-01:
I ended up using threaded inserts instead. The nuts were a bit of a pain

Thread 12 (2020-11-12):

Frontal sensor and camera support not mountable

JonathanMortes, 2020-11-12:
The model does not allow the camera mount to fit into the ultrasonic mount, the camera mount is too thick. Also the Camera support does not fit correctly as it is limited/blocked by the pins, needs extra 2mm clearance.
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

michaelkubina, 2020-11-19:
Hi, concerning the SR04 Ultrasonic Sensors...its a squezing mechanism and it is supposed to remove a little from the wegdes on your cameramount (those on the side, which presss the sonar down). The sonar should not be fully pushed down, when adding the cameramount, but instead should stick out a little...so when you gently press them together you also push your sonars a little bit further down. I had no issues with that. It looks in your final picture, like the sonar is also turned by 180°, so that the clock is on the wrong side and not in its dedicated pocket.

The camera on the other side is weird. I know, that its tight and that there is not much tolerance. But it would not in any way lead to a such big gap. Is it possible, that you use the camera has not the OV2640 Version 2? It has a slightly longer cable...this is the only thing i could think of causing this.

I will flag the camera-mounting-issue as a bug and will look into a possible solution, which does not require a specific cam-version.

michaelkubina, 2020-12-06:
Camera-Mounting Issue solved with last update: https://github.com/michaelkubina/SpotMicroESP32/commit/400f984ac320ee224c66f13d99b1b444cfc76c49

From the looks of it and when simulating the other ESP32-CAM in CAD it results in the same offset as seen in the pictures. I can only believe this was the issue and i updated the camera-parts, to fit both the ESP32-CAM OV2640 Ver.1 and Ver.2

Issue will be closed.

Closed 2020-12-06.

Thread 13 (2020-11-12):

Dual sided cable battery support and motherboard enhancements

JonathanMortes, 2020-11-12:
Hello, may I suggest a dual channel for the 2 cables (power+balancing) for separate cabled batteries. This will utilize the same board but would use the opening. Also, make  it so the top of the internal supporting channel is not closed for easy cable passthrough. Thanks!

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

michaelkubina, 2020-11-19:
Hello Jonathan,

the idea is to have the battery permanently mounted in place and charged via balancer (even though it takes longer) - no need for opening the robot in any way. In the circuitry mountingplate is a small hole, to route your T-Connector extensions out from the bottom to your on-off switch. What you suggest, would require some kind of junction for the cable, where one strand goes into the circuit and one hangs loose for the charging and is being routet in a way, so that its accessable through some hole.

Since thinking of such an solution, designing and prototyping binds a lot of time (which i sadly dont have that much of), i would leave this to others - i think it would be a great mod, but i dont think i will be the one making it. I leave this ticket open for other, who maybe like to go for it.

Closed 2020-12-17.

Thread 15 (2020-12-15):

(New circuitboard needed) New power supply too big for holes also mounting places for CV and CC measurement units needed

JonathanMortes, 2020-12-15:
I suppose they are part of the pending update. For the measurement units I suggest either belly (though it would be too tight) or in the rear as the removal of the TF screen leaves plenty of space. And maybe swap the small DC unit for the big one in terms of placements for better cable management as the new power supply has a big footprint or at least as close to the side as possible.
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

michaelkubina, 2020-12-17:
Hello Jonathan,

yes, this is from the pending parts update - switching positions was my idea as well. Especially because the neopixel-ring is mounted with screws, which otherwise would have touched the coild of the buck-convertert. I have now completed the new mountingplate for the SZBK07 buck converter and i will leave it parallel to the XL4016...both are usefull i think - for MG996Rs or when more power is needed.

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

You can find the part here - i like the extended one more for cable management:
* https://github.com/michaelkubina/SpotMicroESP32/blob/master/parts/SpotMicroESP32_parts_v1_0_0/stl/Circuitry_Mountingplate_SZBK07.stl
* https://github.com/michaelkubina/SpotMicroESP32/blob/master/parts/SpotMicroESP32_parts_v1_0_0/stl/Circuitry_Mountingplate_SZBK07_Extended.stl

Better measure beforehand, if your screwholes are 39mm x 53,5mm apart in this module...i often encountered modules, which have some other configurations and thus other dimensions. Maybe not in this one, but definetl with the LM2596.

The current and voltage sensor units are now placed in the modular rear-cover. I have added the updated parts already to the repo about two weeks ago. This was, when the OLED was installed in the top-cover and the TFT was removed completly from the rear.

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

Maybe you want to check out the new should-joint servomounts as well...they are now reconfigured, so that you route your cables through, preventing them from scrubbing along other edges.

michaelkubina, 2020-12-17:
btw: if you are familiar with freecad, or any other cad, than just open/import the original file for the circuitboard and modify parts of it, if you need special changes (like the hole at your lipo).

Feedback appreciated...wiring might be tricky, because you would need cable-shoes and bend them so that they stand up straight. Proper insulations with shrinking hoses to avoid unwanted short circuits are recommended.

JonathanMortes, 2020-12-17:
Hi Michael,
Thanks for the work and the new parts. Regarding my lipo, I changed it for a bigger one and fits like a charm.

JonathanMortes, 2020-12-17:
Hi Michael,

Thanks for the work and the new parts. Regarding my lipo, I changed it for a bigger one and fits like a charm.

Regarding changes on files, I'm experienced with fusion 360 and Autodesk Inventor, I have not touched FreeCad or found an easy way to import it to them, but I'll give it a go if the SZBK07 module's size isn't a good fit. I was planning regardless on adding a bunch more HW to spot: force sensors on the foot and a couple UltraSound sensors on the sides (maybe belly at an angle) so let me know if you need help with any modeling or if you're interested in such enhancements. (I've yet to decide wether to add the neopixels or not as I haven't found a good one on amazon or seen the effects, maybe if you could post some pics that would be nice).

In terms of the CC/CA sensors. Nice placement. There is a black part or rubber to support one (don't know if its printable or not, just to make my own if so) but I have them already printed.

Finally, ¿have you printed and tested the should-joint servomounts? I was waiting on any changes before printing them as I am not sure about the fit, but if you've done it I'll give it a go!

michaelkubina, 2020-12-18:
The black rubber is just a shrinking hose, that protects the lines on the pcb from the screws scratching them...i had a issue once with the usb ports on my Spotmicro.

The shoulder joint parts are nice, i already printed and use them.
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

Maybe i export all freecad files as step files as well. This way import should be no issue whatsoever, when there is no native import option for freecad files.

Adding more to the spot is always a good idea...we still have plenty of pins left. When using more sonars (or even just with those two) try the Newping.h library (just google it)...it's  really sophisticated.

JonathanMortes, 2021-01-06:
Hello Michael,

I tested those new parts and they work like a Charm #SavedServoWires. Also thanks for the pics on the mounting places for the sensors. My VCC sensor had a weird M1 screw and had to improvise a support fix but they all fit perfectly on the design.

In other news, I remember you were thinking on a solution for unplugging the battery. I joined the male T plug with the main spot power with a screwed double sided cable joint. In case you ever need to dismount spot's power cables and don't want to desolder the deans plug, it comes quite handy as it makes everything power related (except the main pinned power bus) removable without desoldering.

Closed 2021-01-06.

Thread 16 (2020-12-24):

May I use  TD8320MG?

liwenz, 2020-12-24:
Thanks for your share. I have downed all your git .
I have made a robot dog which parts printed from https://www.thingiverse.com/thing:3445283 and mg995 as option.
I hope to change the servo motor as TD8320 as it's 333HZ and mg995 is 50HZ.
The parts need to be edited.The  freecad is used to see and edit.  I found I could not edit the stl file then google here.
I'm a newbee at freecad. Your design is more professional and freecad files are shared 。
May I use your design to assemble TD8320 and MG995?Or which parts  should be edited?
Your assemble is great. Could I have a print parts list file, eg. leg.stl 4 mean 4 legs need to be  printed?

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

michaelkubina, 2020-12-26:
Those dimensions are pretty close to the ones from the MG996R (40.3*20*37)...but the ~2mm in height might be a problem. I cant promise it would work without issues...without rubber dampeners it should most likely fit, with rubber dampeners it can be too tight.

You can find a partlist here: https://github.com/michaelkubina/SpotMicroESP32/tree/master/parts/SpotMicroESP32_parts_v1_0_0

Just dont use deprecated parts and just use one circuitry-mountingplate (choose a suitable one). Apart from that, if really necessary, you would need to edit a lot of parts to make your servos fit. It's not only the servo-pockets in those parts, but the corresponding servohorn-mounts and maybe even screwholes might be in the way....

So with this all in mind, i leave this up to you if you want to try those servos with the risk of not being able to mount them properly. Technical drawings and measurements with calipers are always two different values and experimenting with other parts than those mentioned are your responsibility.

liwenz, 2021-01-18:
Thanks for your answer. I focus on robot's walking and circuits recently. After some time, I could try the new freecad  design.

Sent from Outlook<http://aka.ms/weboutlook>

________________________________
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

Closed 2021-01-15.

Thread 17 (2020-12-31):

Suggested upgrade/bug: Updated top shoulder m3 nut holes kind of tight

JonathanMortes, 2020-12-31:
Hey, maybe look at this one some time.  I fitted only one in the end but it was quite tricky due to there being not much leeway to ease its way (I'm still trying to fit the others but almost 30min in it's getting tedious). Maybe making it slightly wider would help with assembly speed. The bottom shoulder is fine btw. They're both quite the upgrade from previous model.
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g

michaelkubina, 2021-01-06:
Hello Jonathan,

from memory those holes should have the same dimensions in both the top and bottom shoulder block. But memory can be wrong, so i have looked into the FreeCAD-Files and i can confirm the dimesions are exactly the same. I think the issue here is the "elephant foot" effect, when printing (e.g. https://all3dp.com/2/elephant-s-foot-3d-printing-problem-easy-fixes/).

In the bottom part the nutholes are printed later, so they are not the first layer touching the buildplate. But in the top part they are printed with the first layer and thus can be slightly smaller in the first 1-2 layers. The width in both parts is at 5,8mm, but in the top part the first 1-2 layers can be off by a margin due to this effect.

The easiest solution is to scrub the edges of the first layer in the nutholes a little bit - the other option is to get rid of this effect.

JonathanMortes, 2021-01-06:
You're right. I did do those quick fixes but waited for confirmation before closing the issue just in case. And indeed, I started to suffer from elephants foot by progressive misscalibration. I guess it was time to recalibrate after almost a kilogram of PLA printed. Thanks for the suggestion and help, Michael!

Closed 2021-01-06.

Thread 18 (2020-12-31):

Possible upgrade: mounting plate relay holes 1mm wider

JonathanMortes, 2020-12-31:
It seems that in the short version, the relay mounting holes aren't as wide as in the long version making only 2 holes mountable.
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

michaelkubina, 2021-01-06:
Hmm, i was not able to find the problem...in the FreeCAD-Sketches all four mounting-plates (both long/short for XL4016 and SZBK07) have the same dimensions for the pins. They are 28mm x 20mm apart, which fits the relay i have got. In your case it looks like its off by a whole 1mm and i most likely think, that the modules sold in different world regions or from different resellers/manufacturers have slightly different dimensions...

but none the less, i would like to look at it again ... so could you please tell me, which STL you are using and what shorter STL you have used that had a better fit?

JonathanMortes, 2021-01-06:
After comparing with the two previous long XL4016 boards and the current short SZBK07 board, It turns out they are indeed all shorter by that 1mm except for one American relay I've got that does fit as it houses a smaller board. It's also the case for the usb mini mounting holes. I've bought everything from standard retailers on EU via Amazon so I guess its regional. But as every other component fits It's those I guess. If I ever need a 4th version I guess I'll move them and provide the files for those with slightly bigger components as me. Nevertheless, thanks for checking it out and I'm really sorry for the confusion and time spent looking this things up. Let me make it up to you by sharing this simple addition to the project: a pin mounting plate, that fits in the board and serves as a DIY version of the double sided pin soldering board for connections.

[pinSupport.stl.zip](https://github.com/michaelkubina/SpotMicroESP32/files/5778483/pinSupport.stl.zip)
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

jalber2010, 2021-01-08:
Good morning, first of all congratulations on the project and thank you very much for the great work you are doing.
I just wanted to comment that I have exactly the same problem that JonathanMortes previously mentioned. As you can see in the photo the screw holes are misaligned, only two match.
In my case I live in Spain but I ordered the relays from aliexpress china.
Just in case I ordered two different brands, a total of 6 relays and all of them are misaligned. Not a big deal, just a comment.
In my case I am using the design from 22 days ago with the XL4016. Circuitry_Mountingplate.stl.

On the other hand, I think it would be very good if the Circuitry_Mountingplate had holes to pass the cables through the lower part and thus leave the wiring on the upper part a little more clear. It's just a suggestion. At the bottom only the battery goes and there is a lot of space to be able to pass the cables and fasten them with cable ties.
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

michaelkubina, 2021-01-15:
Hello Jalber2010,

thank you for your feedback. I will add the request of widening the distance for the mounting-pins for the relay at about 1mm to my To-Do and will make those changes in the coming ~2 weeks. It seems, that it effect more users, so it seems like a good idea to do this.

The second request...adding some holes to the bottom for cable-routing...well, this is something, that i wont adress actually. With the LiPo in place, there would not be any access from the shoulders sides as it blocks the way ...and routing cables from above under the plate to route them back up seems not benefitial. If you want changes like these, than altering the FreeCAD models i provided to your needs would be the best way to achieve this. This way you can make all modifications you need ;-)

JonathanMortes, 2021-05-13:
I'm redesigning the circuitry mount a bit to add a multiplexor for the I2C channels as well as an arduino nano for force sensor processing and handling all the I2C signals from the different components. And while I'm at it, I've moved the holes 1mm to fix it and I'm also going to move the connections hub and the USB ports to fit the ones I bought which are slightly smaller and need to be higher.

All in all, here is the same sty /step file with the fix. If anyone is interested in the rest of the mods, let me know!

With this I believe the issue is closed.
(please note STL may be displayed on Cura at 100% but in reality it's 10% so scale it to 1000%)
[ReleFixMountingBoard.zip](https://github.com/michaelkubina/SpotMicroESP32/files/6474951/ReleFixMountingBoard.zip)

Closed 2021-05-13.

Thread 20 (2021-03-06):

Circuitboard_Mount (Template).FCStd does not fit (too wide)

YouMakeTech, 2021-03-06:
Circuitboard_Mount (Template).FCStd does not fit. It is too wide: 110 mm instead of 106.5 mm.
I know this file is not supposed to be printed but I am using it because I am trying to build a Raspberry Pi version of the SpotMicroESP32 and wanted to start with a simple plate.
Please find attached the proposed changes.
Best Regards
Vincent

[Circuitboard_Mount (Template) 106.5 mm wide.zip](https://github.com/michaelkubina/SpotMicroESP32/files/6095078/Circuitboard_Mount.Template.106.5.mm.wide.zip)

michaelkubina, 2021-03-06:
You are right, i must have overseen this. I know that this part was off at some point, but i thought i have committed the fix already. Thanks for pointing this out and for updating the part. I will push your updated STL and FreeCAD file immediatly to the repo.

You might also want to consider using the [latest Mountingplate Template](https://github.com/michaelkubina/SpotMicroESP32/blob/master/parts/SpotMicroESP32_parts_v1_0_0/freecad/Circuitry_Mountingplate%20(Template).FCStd) instead or at least take a look at it for inspiration. The one you have is a rudimentary part, that i used, before i designed the charging port for the balance-charger or the usb-ports for flashing. The USB-Ports might be unnecessary, when going with a Raspi, but the balance-charger port might be still of interest. But of course you can just use this template if you want - its just something i wanted to mention ;-)

Closed 2021-03-06.

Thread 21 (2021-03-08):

Rubber Dampeners Question

AugustDG, 2021-03-08:
Hello all!

I'm a student at Dawson College (in Montreal) and I am creating this robot for one of my courses (super excited to do so too 😄) and I had a question about the utility of the rubber dampeners? I have some that came with the servo motors:

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

And I imagine they are some sort of adapters to use with M3 screws (since they don't seem to be able to directly screw into the screwhorn), but I'm not sure what exactly they are and how I would use them? I tried to look it up, but nothing came up on Google...

Any help would be very appreciated!

Otherwise, thank you very much for all the instructions: they are surprisingly clear to read :)

AugustDG, 2021-03-08:
Just saw the dampeners in the CAD model 😅, now know what they're for!

michaelkubina, 2021-03-08:
Thats great, was just going to post a picture. I think they might be referred as dampeners as well...but i am not entirely sure with this. Glad you have found it out by yourself!
I wrote the assembly guide only to realize at a very late stage, that i was missing those in the pictures...added a disclaimer at the beginning for it. Also some steps are for deprecated parts (i left them in there), but the new parts should at least be described via text. If you want, then join the discord and share your progresses! its always intersting to see, how others are doing ;-)

Closed 2021-03-08.

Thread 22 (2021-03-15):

Servo Motor Voltage

Seasandwpy, 2021-03-15:
Hi,
the servo motor is powered by 6.5V voltage with PCA9685 board, but the max V+ voltage for PCA9685 board is 6V. Will this be a problem?

AugustDG, 2021-03-15:
Can I ask why are the servo motors (or where you saw the servo motors) being powered by 6.5V?

Because if you feed more voltage than it's capable, you'll most definitely damage it some way or another...

michaelkubina, 2021-03-15:
Hello @Seasandwpy and @AugustDG,

it is true, that the Servos (MG996R) are powered at 6,5V via the XL4016/SZBK07 Buck-Converters output (passing through a relay if installed). This is because it provides some additional torque+speed and they are capable of handling this voltage.

@AugustDG
Its within specs, even if most sellers talk the rated maximum voltage down for reasons i cant tell. Maybe because they only looked at the stall torque of 11KG*cm at 6.0V in those descriptions. The same applies to the rotation speed, which is described at 4.8V and 6.0V.

If you look at the specs at the TowerPro Homepage, its stated that the maximum operational voltage range is from ~4.8V to 6.6V - [look here](https://www.towerpro.com.tw/product/mg996r/)

@Seasandwpy
The PCA9685 module comes in different configurations. It states on the bottom side that the maximum voltage is 6.0V for V++. Exceeding by 0.5V is not that much and it works in my build without problems...but this is not a reasonably satisfying answer i presume.

The configurations i mentioned are "with polarity protection diode" (never seen one tbh, mine where withoug) and "with capacitor"
- The diode often blows from what i have heard in the channels and actually is not necessary for safe operations - from what i understand its the current, that causes it and not the voltage.
- the ones with a capacitor are only limited by the capacitors rated maximum voltage - often its a 10V 1000uF capacitor or such. So here you can have problems, that you actually exceed ratings, when its a smaller rated one.

The PCA9685 chip itself is only rated up to 5.5V (iirc), but the circuits are sepearated and there is no connection to V++. So no need to worry here and this is also the reason, why 6V max does not make so much sense to me. The powerlines on the pcb can handle higher voltage and only with high currents you should expects problems.

A common mod is to enhance the power-rails (V++ & GND) from the terminal block to the pins (underside of the pins) of the channels with solid copper wires, so that the module itself can handle the high currents better. But thats basically it...

So, the answer i can give: There are good reasons, why 6.5V should not be problematic. If you are unsure, than simply go with 6V...and if you feel comfortable, then increase with 0.1V steps or so until you reach a (imo) safe max of 6.5V.

AugustDG, 2021-03-15:
Great detailed response and thank you! 😁

JonathanMortes, 2021-06-28:
Hi, I'm using 6.5V on the PCA9685 with no problems found. Many servos use 6V for their optimal power and giving them extra juice (+0,5V) is more than safe. Just provide them with enough current or the robot will stall. I believe this issue should be closed.

liwenz, 2021-08-18:
In PCA9685, there are Vcc and V+.  They are different, V+ is for Servo , maybe 6.5V or 8.4V or other. Vcc is for PCA chip and it should be max V is 6V.
How do you choose your battery?
1.2V x 5 or 6 is good for V, but the amp is not enough. 3.7V x 2 =7.4V and maybe 8.4V , but mg995 is only 6-7.2V. I use two diode to low the voltage.
I prefer to 8.4v servo and it does not need to low voltage. eg cls6336hv(expensie), hv5523mg(some cheap)

mattwilliamson, 2023-06-26:
> In PCA9685, there are Vcc and V+. They are different, V+ is for Servo , maybe 6.5V or 8.4V or other. Vcc is for PCA chip and it should be max V is 6V. How do you choose your battery? 1.2V x 5 or 6 is good for V, but the amp is not enough. 3.7V x 2 =7.4V and maybe 8.4V , but mg995 is only 6-7.2V. I use two diode to low the voltage. I prefer to 8.4v servo and it does not need to low voltage. eg cls6336hv(expensive), hv5523mg(some cheap)

@liwenz What diodes did you use? I ordered some 15A on Amazon, but they only drop .136v each.

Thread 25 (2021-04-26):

Front and rear cover assembly instructions need to be reworked!

AugustDG, 2021-04-26:
Just a friendly reminder that most of the front and rear cover sections are using deprecated parts and should probably be redone! :D

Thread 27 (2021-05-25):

PWM Servo calibration

JonathanMortes, 2021-05-25:
Hey,

been trying to do the servo calibration with no results. Is there anyway you can share your numbers for ds3218mg and possibly the code used? (Seen and used the one mentioned on the guide but it doesn't do anything. Any help would be greatly appreciated.

Thanks in advance Michael!

Closed 2021-06-10.

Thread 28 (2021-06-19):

CAM with TTL

JonathanMortes, 2021-06-19:
Hi Michael, with the current circuit layout, how have you overcomed the programming and usage of the cam. Currently I'm unable to, without a jumper wire from GPIO 0 to GND, program the board. Then I need to take it out to use it.
Any help is welcomed

michaelkubina, 2021-06-20:
Hi, i see that it is only mentioned in the Fritzing diagram and i think you might have closed this issue already, because you have become aware of it. I had researched a while before i actually found a solution for this problem. Because as you say, it would have meant to either route the jumper out of the body or to look for a different way like OTA flashing, once it has been flashed with a suitable firmware for this.

I will leave a link here, from where i got my solution...maybe helpful as a insight as well: https://github.com/raphaelbs/esp32-cam-ai-thinker/issues/32

Usage of the CAM btw is as a separate entity...like having two devices in you wireless network. I like this firmware as a start: https://github.com/easytarget/esp32-cam-webserver/

Goodbye :-)

JonathanMortes, 2021-06-20:
Hi Michael! I did not succeed because of the missing RST wire to GPO0 I could not solder a while back, yesterday I succeeded  and after some rewiring, got it to work. I'm also using the Cam as an independent device although it's still wired to the main ESP32 board (maybe it'll be useful at some point. Thanks for the tips by the way!

This is my current setup:

[circuito_v6_ALFREDog.pdf](https://github.com/michaelkubina/SpotMicroESP32/files/6682053/circuito_v6_ALFREDog.pdf)

I've been adding some extra things for more advanced control. I'm presenting the software and control programs as part of my master's  degree final project and I will propose creating a new branch with you with the updated components, designs and most importantly, software. At least its offering some more alternatives with the same base parts. I've even got an alternative version with a custom ultra sonic 360º radar mounted on top

Thanks again for the feedback and work!

Closed 2021-06-19.

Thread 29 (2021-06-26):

Short circuit

JonathanMortes, 2021-06-26:
Hey Michael,

I've been having issues with short circuits with the current schematic. Have you had them? Could you share current wiring in photo? I'm seeing it pop up whenever the rele activates in cycles. (I've had a couple of smoky incidents too. Appreciate your or anyone's insight

michaelkubina, 2021-06-28:
Hi Jonathan,
i had not encountered any short circuits with this schematic. But i have heard of blown PCA9685...or to be more precise of the polarity protection diodes, which some modules have and others dont. And the capacitor might blow when either stressed over spec (normaly 10V 100(0?)uF iirc). But if it blows, its rather because of reversed polarity i would assume...apart from this part, which seems to be a weak spot in many builds (not only spotmicro, but other bots as well), i have not heard of any issues.

Here are some pictures of my current wiring, i hope they allow for some insight:

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

JonathanMortes, 2021-06-28:
Hi Michael, thanks for the answer and pics!  Turns out it was a mix of the PCA and the Step down that also fried 1 ESP and damaged another ADC (although it may be just defective as it still works). The only thing that strikes me is the current and voltage sensor which work great separated from the circuit but not when incorporated. Nevertheless, after fixing that and a whole lot of cables and servo angles. I've got my version working! Added 4 MPUs, an I2C mux, 4 pressure sensors and a RPi ZW for RL control based on 12-point bezier curves for gait. What I strongly suggest is investing on some metal round servo horns as they really tend to break and unless you print PETG or high ABS, the PLA just gets too much backlash to be controlable and simply breaks.

Closed 2021-06-28.

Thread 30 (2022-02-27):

Question on hardware components

liamhan0905, 2022-02-27:
Could you explain what this circular circuit is on the first image? What's it used for?

Also, what is this 3 pins on the 2nd picture?

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

JonathanMortes, 2022-02-27:
Hi, first is led lights which are deprecated. Second is the lipo 2s
charging cable that runs from the belly mounting point to the back (top
case) for easy charging)

El El dom, 27 feb 2022 a las 9:33, Liam Han ***@***.***>
escribió:

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

liamhan0905, 2022-02-27:
I see thank you for the clear explanation. Could you also add a diagram of how the microusb is connected to other devices? The schema that you provided does not have this detail.

Also, how is SZBK07 with Extensions different to the one without extension? I see that it just has two extended "beam" at each end but the mountingplate itself are the same size. So I'm confused what the purpose of this extension is.

Lastly, do you have a .ipt file of the mounting plate? I am planning to add a raspberry pi in addition to run ROS on it. And I'd like to make a mod. Thank you!

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

michaelkubina, 2022-03-02:
The micro-usb has 4-5 pads. GND, VCC, D+, D- and in some cases ID/SENSE (for OTG-Devices). I have cut a micro-usb cable for the esp32 to length and soldered the corresponding wirs to the pads on the micro-usb-pcb. I did the same for the Mini-USB-cable that i cut to length for the serial-flasher for the esp32-cam. Be careful not to short the wires when screwing the screws in. I used shrinking hose to protect them...

The "beams" are the extensions...for the neo-pixel LEDs i mentioned (the underperforming, deprecated underglow). thats basically it...you can use it for cable-management if you like, but you dont need them...otherwise the SZBK07 fits this specific DC-DC converter, which would be better suited when you use stronger servos.

I dont know which software uses the *ipt format, but i have provided all models as FreeCAD-Files, so you can make you own modifications. I believe, i also made a raspberry pi zero mod (no support here from my side, not tested since i dont own one), which is in the mods-folder in this repo -> also check out, if you dont want to use the reinforced shoulder mod, but you would need to print other shells for the legs. https://github.com/michaelkubina/SpotMicroESP32/tree/master/parts/SpotMicroESP32_parts_v1_0_0/mods

If you want to use another raspberry than the zero, then you would need to download FreeCAD and do your changes there. Or you export the models as STEP-Files and import them into your workflow. Maybe other formats are also supported, but since i only design in FreeCAD i have no insight on this.

Best regards!

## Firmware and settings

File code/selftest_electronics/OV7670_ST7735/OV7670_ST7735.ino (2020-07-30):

//*************************************************************************
//	OV7670 (non FIFO) Sample program for ESP32 
//
//  OUTPUT:	ILI9341 TFT(320x240) SPI 
//					option XPT2046 Touchscreen
//
//*************************************************************************

/*************************************************************
 * 
 * Libraries
 * 
*************************************************************/

#include <Arduino.h>
#include <Wire.h>
#include <SPI.h>
#include <Adafruit_SPITFT.h>
#include <Adafruit_PWMServoDriver.h>
#include "OV7670.h"
#include <Adafruit_GFX.h>
#include <Adafruit_ST7735.h> // Hardware-specific library
#include <Adafruit_ST77xx.h> // Hardware-specific library
#include <Adafruit_ST7789.h> // Hardware-specific library for ST7789

/*************************************************************
 * 
 * HC-SR04 Ultrasonic Range Sensor
 * 
*************************************************************/

#define SONAR_TRIG_LEFT   2
#define SONAR_ECHO_LEFT   15

long sonar_duration_left = 0;
long sonar_distance_left = 0;

/*************************************************************
 * 
 * HC-SR04 Ultrasonic Range Sensor
 * 
*************************************************************/

#define SONAR_TRIG_RIGHT   2
#define SONAR_ECHO_RIGHT   16

long sonar_duration_right = 0;
long sonar_distance_right = 0;

/*************************************************************
 * 
 * HW-482 5V Relais
 * 
*************************************************************/

#define RELAIS   13

bool RELAIS_STATE = false;


/*************************************************************
 * 
 * 1.77" TFT with LED Backlight
 * 
*************************************************************/

// For the Adafruit shield, these are the default.
/*const int TFT_RS = 5;
const int TFT_CS = 17; 
const int TFT_SDA = 18; 
const int TFT_SCL = 19; 
#define TFT_LED   16*/
const int TFT_RS = 17;
const int TFT_CS = 5; //HW SPI
const int TFT_SDA = 23; //HW SPI
const int TFT_SCL = 18; //HW SPI
#define TFT_LED   19
#define TFT_RES   -1  // Reset physicaly connected to EN (enabled), -1 required by TFT library

const int TFT_LED_PWM_CHANNEL     = 5;
const int TFT_LED_PWM_RESOLUTION  = 8;
const int TFT_LED_PWM_FREQUENCY   = 5000;
      int TFT_LED_PWM_DUTY        = 255;

/*************************************************************
 * 
 * POWER BUTTON with integrated LED
 * 
*************************************************************/

#define PWR_BTN       4
#define PWR_BTN_LED   0 // PWM during boot wont do anything, since RTC GPIO -> used as External Wake Up (ext0)

int PWR_BTN_STATE = 0;

const int PWR_BTN_LED_PWM_CHANNEL     = 4;
const int PWR_BTN_LED_PWM_RESOLUTION  = 8;
const int PWR_BTN_LED_PWM_FREQUENCY   = 5000;
      int PWR_BTN_LED_PWM_DUTY        = 255;

/*************************************************************
 * 
 * OV7670 Camera Module without FIFO
 * 
*************************************************************/
uint16_t *buf;

const camera_config_t cam_conf = {
	.D0	= 36,
	.D1 = 39,
	.D2 = 34,
	.D3 = 35,
	.D4 = 32,
	.D5 = 33,
	.D6 = 25,
	.D7 = 26,
	.XCLK = 12,
	.PCLK = 14,
	.VSYNC = 27,
	.xclk_freq_hz = 12000000,			// XCLK 10MHz
	.ledc_timer		= LEDC_TIMER_0,
	.ledc_channel = LEDC_CHANNEL_0	
};
//	SSCB_SDA(SIOD) 	--> 21(ESP32)
//	SSCB_SCL(SIOC) 	--> 22(ESP32)
//	RESET   --> 3.3V
//	PWDN		--> GND
//	HREF		--> NC

/*************************************************************
 * 
 * GY-521 Gyroscope/Acceleration Sensor (front)
 * 
*************************************************************/

bool GYRO_FRONT_STATE = false;

int16_t gyro_front_acx = 0;
int16_t gyro_front_acy = 0;
int16_t gyro_front_acz = 0;

int16_t gyro_front_gyx = 0;
int16_t gyro_front_gyy = 0;
int16_t gyro_front_gyz = 0;

int16_t gyro_front_tmp = 0;

/*************************************************************
 * 
 * GY-521 Gyroscope/Acceleration Sensor (rear)
 * 
*************************************************************/

bool GYRO_REAR_STATE = false;

int16_t gyro_rear_acx = 0;
int16_t gyro_rear_acy = 0;
int16_t gyro_rear_acz = 0;

int16_t gyro_rear_gyx = 0;
int16_t gyro_rear_gyy = 0;
int16_t gyro_rear_gyz = 0;

int16_t gyro_rear_tmp = 0;

/*************************************************************
 * 
 * PCA9685 12Bit 16Ch PWM-Servomodule
 * 
*************************************************************/

bool PWM_SERVO_STATE = false;

/*************************************************************
 * 
 * I2C TwoWire
 * 
*************************************************************/

#define I2C_SCL   22
#define I2C_SDA   21
#define I2C_FRQ   400000

bool I2C_STATE = false;

/*************************************************************
 * 
 * I2C Adresses
 * 
*************************************************************/

#define PWM_SERVO_ADDR    0x40

#define GYRO_FRONT_ADDR   0x68
#define GYRO_REAR_ADDR    0x69  // ad0 pin connected to 3v3

#define CAM_WRITE_ADDR    0x42
#define CAM_READ_ADDR     0x43

/*************************************************************
 * 
 * Objects
 * 
*************************************************************/

//TwoWire I2C = TwoWire(0);

Adafruit_ST7735 tft = Adafruit_ST7735(TFT_CS,  TFT_RS, TFT_SDA, TFT_SCL, 0);
//Adafruit_ST7735 TFT = Adafruit_ST7735(TFT_CS, TFT_RS, TFT_SDA, TFT_SCL, TFT_RES);
//Adafruit_PWMServoDriver PWM = Adafruit_PWMServoDriver(PWM_SERVO_ADDR, I2C);
Adafruit_PWMServoDriver PWM = Adafruit_PWMServoDriver(PWM_SERVO_ADDR);
OV7670 cam;						// camera

/*************************************************************
 * 
 * Other
 * 
*************************************************************/

int pos = 0;
int duty = 0;

/*************************************************************
 * 
 * ### SETUP ###
 * 
*************************************************************/

void setup() {

  /*************************************************************
   * 
   * PinModes
   * 
  *************************************************************/

  // HC-SR04 Ultrasonic Range Sensor
  pinMode(SONAR_TRIG_LEFT, OUTPUT);
  pinMode(SONAR_ECHO_LEFT, INPUT);

  pinMode(SONAR_TRIG_RIGHT, OUTPUT);
  pinMode(SONAR_ECHO_RIGHT, INPUT);

  // HW-482 5V Relais
  pinMode(RELAIS, OUTPUT);

  // 1.77" TFT with LED Backlight
  pinMode(TFT_LED, OUTPUT);
  ledcSetup(TFT_LED_PWM_CHANNEL, TFT_LED_PWM_FREQUENCY, TFT_LED_PWM_RESOLUTION);
  ledcAttachPin(TFT_LED,TFT_LED_PWM_CHANNEL);

  // POWER BUTTON with integrated LED
  pinMode(PWR_BTN_LED, OUTPUT);
  pinMode(PWR_BTN, INPUT_PULLDOWN);
  ledcSetup(PWR_BTN_LED_PWM_CHANNEL, PWR_BTN_LED_PWM_FREQUENCY, PWR_BTN_LED_PWM_RESOLUTION);
  ledcAttachPin(PWR_BTN_LED,PWR_BTN_LED_PWM_CHANNEL);

  /*************************************************************
   * 
   * I2C
   * 
  *************************************************************/

  Wire.begin(21, 22);
  Wire.begin();
  Wire.setClock(400000);

  // Initialize I2C Bus
  
  //I2C_STATE = I2C.begin(I2C_SDA, I2C_SCL, I2C_FRQ);

  // 12-Bit 16 Channel PWM Module

  PWM.begin();
  PWM.setPWMFreq(50);

  // Gyroscopes
/*
  I2C.beginTransmission(GYRO_FRONT_ADDR);
  I2C.write(0x6B);  // PWR_MGMT_1 register
  I2C.write(0);     // set to zero (wakes up the MPU-6050)
  I2C.endTransmission(true);

  I2C.beginTransmission(GYRO_REAR_ADDR);
  I2C.write(0x6B);  // PWR_MGMT_1 register
  I2C.write(0);     // set to zero (wakes up the MPU-6050)
  I2C.endTransmission(true);
*/
    Wire.beginTransmission(GYRO_FRONT_ADDR);
  Wire.write(0x6B);  // PWR_MGMT_1 register
  Wire.write(0);     // set to zero (wakes up the MPU-6050)
  Wire.endTransmission(true);

  Wire.beginTransmission(GYRO_REAR_ADDR);
  Wire.write(0x6B);  // PWR_MGMT_1 register
  Wire.write(0);     // set to zero (wakes up the MPU-6050)
  Wire.endTransmission(true);

  /*************************************************************
   * 
   * 1.77" TFT with background illumination
   * 
  *************************************************************/
  tft.initSPI(40000000);
  tft.initR(INITR_BLACKTAB);
  tft.setRotation(1);
  tft.fillScreen(ST77XX_BLACK);

  /*************************************************************
   * 
   * Serial Output
   * 
  *************************************************************/

  Serial.begin(115200);
  Serial.println("< ESP32 DevKitC is ready >");
  Serial.println("");

  // I2C
  /*
  Serial.print("I2C Initialization: ");
  if(I2C_STATE){
    Serial.println("PASSED");
  } else {
    Serial.println("FAILED");
  }*/
	
  Serial.println("OV7670 camera Init...");     
  esp_err_t err = cam.init(&cam_conf, QQVGA, RGB565);		// カメラを初期化
  //esp_err_t err = cam.init(&cam_conf, QQCIF, RGB565);    // カメラを初期化
	if(err != ESP_OK)		Serial.println("cam.init ERROR");

	cam.setPCLK(2, DBLV_CLK_x4);	// PCLK 設定 : 10MHz / (pre+1) * 4 --> 13.3MHz  
	cam.vflip( false );		// 画面１８０度回転
 
  Serial.printf("cam MID = %X\n\r",cam.getMID());
  Serial.printf("cam PID = %X\n\r",cam.getPID());

//	cam.colorbar(true);			// カラーバーを表示する場合

}

void loop(void) {
    Serial.println("Making LED glow (TFT & PWR)");
  ledcWrite(TFT_LED_PWM_CHANNEL, TFT_LED_PWM_DUTY);
  ledcWrite(PWR_BTN_LED_PWM_CHANNEL, PWR_BTN_LED_PWM_DUTY);
  Serial.println("Starting Loop");

	while(1){
		for( int y = 0; y < 40; y++){			
			buf = cam.getLine( (y*3)+1 );								// カメラから１ライン分読み込む LineNo(1~240)
			tft.drawRGBBitmap( 0, y*3, buf, 160, 1);	// TFT に１ライン出力
  	}
   for( int y = 0; y < 40; y++){     
      buf = cam.getLine( (y*3)+2 );               // カメラから１ライン分読み込む LineNo(1~240)
      tft.drawRGBBitmap( 0, y*3+1, buf, 160, 1);  // TFT に１ライン出力
    }
    for( int y = 0; y < 40; y++){     
      buf = cam.getLine( (y*3)+3 );               // カメラから１ライン分読み込む LineNo(1~240)
      tft.drawRGBBitmap( 0, y*3+2, buf, 160, 1);  // TFT に１ライン出力
    }    
    
    // put your main code here, to run repeatedly:
     Serial.println("Reading Gyro");
  readGyro();
  Serial.println("Reading Sonar");
  readSonar();
  Serial.println("Printing Status Screen");
  printStatusScreen();
  Serial.println("Checking for Serial Input");
  checkSerialInput();
  Serial.println("Doing the PWM Servo Magic");
  writePWM();

// ### TESTING FROM HERE ###


Serial.println("Reading Power Button Input");
  readPowerButton();
	}
 }

/* void readGyro() {
  Serial.println("### READING GYRO SENSORS ###");
  
  // GYRO FRONT
  I2C.beginTransmission(GYRO_FRONT_ADDR);
  I2C.write(0x3B);  // starting with register 0x3B (ACCEL_XOUT_H)
  I2C.endTransmission(false);
  I2C.requestFrom(GYRO_FRONT_ADDR,14,true);  // request a total of 14 registers
  gyro_front_acx=I2C.read()<<8|I2C.read();  // 0x3B (ACCEL_XOUT_H) & 0x3C (ACCEL_XOUT_L)    
  gyro_front_acy=I2C.read()<<8|I2C.read();  // 0x3D (ACCEL_YOUT_H) & 0x3E (ACCEL_YOUT_L)
  gyro_front_acz=I2C.read()<<8|I2C.read();  // 0x3F (ACCEL_ZOUT_H) & 0x40 (ACCEL_ZOUT_L)
  gyro_front_tmp=I2C.read()<<8|I2C.read();  // 0x41 (TEMP_OUT_H) & 0x42 (TEMP_OUT_L)
  gyro_front_gyx=I2C.read()<<8|I2C.read();  // 0x43 (GYRO_XOUT_H) & 0x44 (GYRO_XOUT_L)
  gyro_front_gyy=I2C.read()<<8|I2C.read();  // 0x45 (GYRO_YOUT_H) & 0x46 (GYRO_YOUT_L)
  gyro_front_gyz=I2C.read()<<8|I2C.read();  // 0x47 (GYRO_ZOUT_H) & 0x48 (GYRO_ZOUT_L)
  Serial.print("Front: AcX = "); Serial.print(gyro_front_acx);
  Serial.print(" | AcY = "); Serial.print(gyro_front_acy);
  Serial.print(" | AcZ = "); Serial.print(gyro_front_acz);
  Serial.print(" | Tmp = "); Serial.print(gyro_front_tmp/340.00+36.53);  //equation for temperature in degrees C from datasheet
  Serial.print(" | GyX = "); Serial.print(gyro_front_gyx);
  Serial.print(" | GyY = "); Serial.print(gyro_front_gyy);
  Serial.print(" | GyZ = "); Serial.println(gyro_front_gyz);
  delay(333);

  // GYRO REAR
  I2C.beginTransmission(GYRO_REAR_ADDR);
  I2C.write(0x3B);  // starting with register 0x3B (ACCEL_XOUT_H)
  I2C.endTransmission(false);
  I2C.requestFrom(GYRO_REAR_ADDR,14,true);  // request a total of 14 registers
  gyro_rear_acx=I2C.read()<<8|I2C.read();  // 0x3B (ACCEL_XOUT_H) & 0x3C (ACCEL_XOUT_L)    
  gyro_rear_acy=I2C.read()<<8|I2C.read();  // 0x3D (ACCEL_YOUT_H) & 0x3E (ACCEL_YOUT_L)
  gyro_rear_acz=I2C.read()<<8|I2C.read();  // 0x3F (ACCEL_ZOUT_H) & 0x40 (ACCEL_ZOUT_L)
  gyro_rear_tmp=I2C.read()<<8|I2C.read();  // 0x41 (TEMP_OUT_H) & 0x42 (TEMP_OUT_L)
  gyro_rear_gyx=I2C.read()<<8|I2C.read();  // 0x43 (GYRO_XOUT_H) & 0x44 (GYRO_XOUT_L)
  gyro_rear_gyy=I2C.read()<<8|I2C.read();  // 0x45 (GYRO_YOUT_H) & 0x46 (GYRO_YOUT_L)
  gyro_rear_gyz=I2C.read()<<8|I2C.read();  // 0x47 (GYRO_ZOUT_H) & 0x48 (GYRO_ZOUT_L)
  Serial.print("Rear:  AcX = "); Serial.print(gyro_rear_acx);
  Serial.print(" | AcY = "); Serial.print(gyro_rear_acy);
  Serial.print(" | AcZ = "); Serial.print(gyro_rear_acz);
  Serial.print(" | Tmp = "); Serial.print(gyro_rear_tmp/340.00+36.53);  //equation for temperature in degrees C from datasheet
  Serial.print(" | GyX = "); Serial.print(gyro_rear_gyx);
  Serial.print(" | GyY = "); Serial.print(gyro_rear_gyy);
  Serial.print(" | GyZ = "); Serial.println(gyro_rear_gyz);
  delay(333);

  Serial.println();
}
*/

void readGyro() {
  Serial.println("### READING GYRO SENSORS ###");
  
  // GYRO FRONT
  Wire.beginTransmission(GYRO_FRONT_ADDR);
  Wire.write(0x3B);  // starting with register 0x3B (ACCEL_XOUT_H)
  Wire.endTransmission(false);
  Wire.requestFrom(GYRO_FRONT_ADDR,14,true);  // request a total of 14 registers
  gyro_front_acx=Wire.read()<<8|Wire.read();  // 0x3B (ACCEL_XOUT_H) & 0x3C (ACCEL_XOUT_L)    
  gyro_front_acy=Wire.read()<<8|Wire.read();  // 0x3D (ACCEL_YOUT_H) & 0x3E (ACCEL_YOUT_L)
  gyro_front_acz=Wire.read()<<8|Wire.read();  // 0x3F (ACCEL_ZOUT_H) & 0x40 (ACCEL_ZOUT_L)
  gyro_front_tmp=Wire.read()<<8|Wire.read();  // 0x41 (TEMP_OUT_H) & 0x42 (TEMP_OUT_L)
  gyro_front_gyx=Wire.read()<<8|Wire.read();  // 0x43 (GYRO_XOUT_H) & 0x44 (GYRO_XOUT_L)
  gyro_front_gyy=Wire.read()<<8|Wire.read();  // 0x45 (GYRO_YOUT_H) & 0x46 (GYRO_YOUT_L)
  gyro_front_gyz=Wire.read()<<8|Wire.read();  // 0x47 (GYRO_ZOUT_H) & 0x48 (GYRO_ZOUT_L)
  Serial.print("Front: AcX = "); Serial.print(gyro_front_acx);
  Serial.print(" | AcY = "); Serial.print(gyro_front_acy);
  Serial.print(" | AcZ = "); Serial.print(gyro_front_acz);
  Serial.print(" | Tmp = "); Serial.print(gyro_front_tmp/340.00+36.53);  //equation for temperature in degrees C from datasheet
  Serial.print(" | GyX = "); Serial.print(gyro_front_gyx);
  Serial.print(" | GyY = "); Serial.print(gyro_front_gyy);
  Serial.print(" | GyZ = "); Serial.println(gyro_front_gyz);
  delay(333);

  // GYRO REAR
  Wire.beginTransmission(GYRO_REAR_ADDR);
  Wire.write(0x3B);  // starting with register 0x3B (ACCEL_XOUT_H)
  Wire.endTransmission(false);
  Wire.requestFrom(GYRO_REAR_ADDR,14,true);  // request a total of 14 registers
  gyro_rear_acx=Wire.read()<<8|Wire.read();  // 0x3B (ACCEL_XOUT_H) & 0x3C (ACCEL_XOUT_L)    
  gyro_rear_acy=Wire.read()<<8|Wire.read();  // 0x3D (ACCEL_YOUT_H) & 0x3E (ACCEL_YOUT_L)
  gyro_rear_acz=Wire.read()<<8|Wire.read();  // 0x3F (ACCEL_ZOUT_H) & 0x40 (ACCEL_ZOUT_L)
  gyro_rear_tmp=Wire.read()<<8|Wire.read();  // 0x41 (TEMP_OUT_H) & 0x42 (TEMP_OUT_L)
  gyro_rear_gyx=Wire.read()<<8|Wire.read();  // 0x43 (GYRO_XOUT_H) & 0x44 (GYRO_XOUT_L)
  gyro_rear_gyy=Wire.read()<<8|Wire.read();  // 0x45 (GYRO_YOUT_H) & 0x46 (GYRO_YOUT_L)
  gyro_rear_gyz=Wire.read()<<8|Wire.read();  // 0x47 (GYRO_ZOUT_H) & 0x48 (GYRO_ZOUT_L)
  Serial.print("Rear:  AcX = "); Serial.print(gyro_rear_acx);
  Serial.print(" | AcY = "); Serial.print(gyro_rear_acy);
  Serial.print(" | AcZ = "); Serial.print(gyro_rear_acz);
  Serial.print(" | Tmp = "); Serial.print(gyro_rear_tmp/340.00+36.53);  //equation for temperature in degrees C from datasheet
  Serial.print(" | GyX = "); Serial.print(gyro_rear_gyx);
  Serial.print(" | GyY = "); Serial.print(gyro_rear_gyy);
  Serial.print(" | GyZ = "); Serial.println(gyro_rear_gyz);
  delay(333);

  Serial.println();
}

void readSonar(){
  Serial.println("### READING ULTRASONIC SENSOR LEFT ###");
  
  digitalWrite(SONAR_TRIG_LEFT, LOW);
  delayMicroseconds(5);
  digitalWrite(SONAR_TRIG_LEFT, HIGH);
  delayMicroseconds(10);
  digitalWrite(SONAR_TRIG_LEFT, LOW);

  sonar_duration_left = pulseIn(SONAR_ECHO_LEFT, HIGH);
  sonar_duration_left = (sonar_duration_left/2) / 29.1;     // Divide by 29.1 or multiply by 0.0343
  Serial.print(sonar_duration_left);
  Serial.println("cm");

  Serial.println();

  delay(200);

  Serial.println("### READING ULTRASONIC SENSOR RIGHT ###");
  
  digitalWrite(SONAR_TRIG_RIGHT, LOW);
  delayMicroseconds(5);
  digitalWrite(SONAR_TRIG_RIGHT, HIGH);
  delayMicroseconds(10);
  digitalWrite(SONAR_TRIG_RIGHT, LOW);

  sonar_duration_right = pulseIn(SONAR_ECHO_RIGHT, HIGH);
  sonar_duration_right = (sonar_duration_right/2) / 29.1;     // Divide by 29.1 or multiply by 0.0343
  Serial.print(sonar_duration_right);
  Serial.println("cm");

  Serial.println();
}

void readPowerButton(){
  PWR_BTN_STATE = digitalRead(PWR_BTN);
  if (PWR_BTN_STATE == HIGH) {
    RELAIS_STATE = !RELAIS_STATE;
    Serial.println("Pushbutton HIGH");
    Serial.print("Relais-State at: ");
    Serial.println(RELAIS_STATE);
  }
  if (PWR_BTN_STATE == LOW) {
    Serial.println("Pushbutton LOW");
  }
  delay(100);
  
  if (RELAIS_STATE == false) {
  Serial.println("Relais-Pin LOW");
  digitalWrite(RELAIS, LOW);
  }
  else {
  Serial.println("Relais-Pin HIGH");
  digitalWrite(RELAIS, HIGH);
  }
}

void printStatusScreen(){
  tft.setTextColor(ST77XX_WHITE, ST77XX_BLACK);

  tft.drawRect(1, 1, 157, 13, ST77XX_WHITE);
  tft.setCursor(3,3);
  tft.println("SpotMicroAIoT");

  tft.drawRect(1, 15, 157, 110, ST77XX_WHITE);
  tft.setCursor(3, 17);
  tft.println("by MiKu");
}

void checkSerialInput(){
    if (Serial.available() > 0) {
      char symbol = Serial.read();
      Serial.print(symbol);
    switch (symbol) {
      case 'e':
        RELAIS_STATE = true;
        break;
      case 'q':
        RELAIS_STATE = false;
        break;
      case 'a':
        pos = 0;
        break;
      case 's':
        pos = 90;
        break;
      case 'd':
        pos = 180;
        break;
      case 'w':
      if (pos < 180) {
        pos += 15;
      }
        break;
      case 'x':
        if (pos > 0) {
        pos -= 15;
      }
        break;
    }
  }
}

void writePWM(){
  PWM.setPWM(0, 0, pos+75);
  PWM.setPWM(1, 0, pos+175);
  PWM.setPWM(2, 0, pos+75);
}

void SetServoPos(float pos)
{
    uint32_t duty = ((400.0/180.0)*pos) + 75;
         // convert 0-180 degrees to 0-4096

        // set channel to pos
        Serial.print("Duty: ");
   Serial.println(duty);
}

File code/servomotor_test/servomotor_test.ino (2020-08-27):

//***********
// Servo motor test
// SDA - pin next to GND - 21
// SCL - 22
//************


#include <Arduino.h>
#include <Wire.h>
#include <Adafruit_PWMServoDriver.h>
#include <CommandParser.h>

#define PWM_SERVO_ADDR    0x40
Adafruit_PWMServoDriver PWM = Adafruit_PWMServoDriver(PWM_SERVO_ADDR);


typedef CommandParser<> MyCommandParser;
MyCommandParser servoCommandParser;
int pulse = 170;
int servo_id = 0;



// the setup function runs once when you press reset or power the board
void setup() {
  // initialize digital pin LED_BUILTIN as an output.
  pinMode(LED_BUILTIN, OUTPUT);

  // 12-Bit 16 Channel PWM Module

  PWM.begin();
  PWM.setPWMFreq(50);

  Serial.begin(115200);

  while (!Serial);

  servoCommandParser.registerCommand("s", "uu", &cmd_servo);
  Serial.println("registered command: s <uint64> <uint64> ");
  Serial.println("example: s 0 150");
  servoCommandParser.registerCommand("sleep", "", &servosSleep);
  Serial.println("registered command: sleep ");
  servoCommandParser.registerCommand("wake", "", &servosWake);
  Serial.println("registered command: wake ");
  Serial.println("");
}

// the loop function runs over and over again forever
void loop() {
  digitalWrite(LED_BUILTIN, HIGH);   // turn the LED on (HIGH is the voltage level)
  delay(100);                       // wait for a second
  digitalWrite(LED_BUILTIN, LOW);    // turn the LED off by making the voltage LOW
  delay(100);                       // wait for a second

  if (checkSerialInput())
    writePWM();
}

void cmd_servo(MyCommandParser::Argument *args, char *response) {
  servo_id = args[0].asInt64;
  pulse = args[1].asInt64;
  strlcpy(response, "success", MyCommandParser::MAX_RESPONSE_SIZE);
}

bool checkSerialInput(){
  if (Serial.available()) {
    char line[128];
    size_t lineLength = Serial.readBytesUntil('\n', line, 127);
    line[lineLength] = '\0';

    char response[MyCommandParser::MAX_RESPONSE_SIZE];
    servoCommandParser.processCommand(line, response);
    Serial.println(response);

    if (strcmp(response, "success") == 0)
      return true;
  }

  return false;
//    if (Serial.available() > 0) {
//      char symbol = Serial.read();
//      Serial.print(symbol);
//    switch (symbol) {
//      case '0':
//        pos = 0;
//        break;
//      case '3':
//        pos = 30;
//        break;
//      case '9':
//        pos = 90;
//        break;
//      case '5':
//        pos = 150;
//        break;
//      case '8':
//        pos = 180;
//        break;
//      case '+':
//        pos += 5;
//        break;
//      case '-':
//        pos -= 5;
//        break;
//    }
//  }
}

void servosSleep(MyCommandParser::Argument *args, char *response) {
  PWM.sleep();
}

void servosWake(MyCommandParser::Argument *args, char *response) {
  PWM.wakeup();
}

void writePWM(){
  Serial.printf("Servo %d: Pulse %d\n", servo_id, pulse);
  PWM.setPWM(servo_id, 0, pulse);
  
}

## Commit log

2020-07-30 Added STLs, FreeCAD-Files, Pinout-File, Filament-Calculations and Selftest-Arduino-Sketch
    [Bottom_Cover (Template).FCStd, Bottom_Cover (Template).stl, Bottom_Cover_Split_Front.FCStd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]
2020-08-02 update 3d printing partlist
    [Bottom_Cover (Template).FCStd, Bottom_Cover (Template).stl, Bottom_Cover_Split_Front.FCStd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]
2020-08-05 added BOM to README.md
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2020-08-10 added assembly guide with first steps
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2020-08-11 corrected assembly guide of lower leg
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2020-08-13 added upper leg to assembly guide, improved clarity
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2020-08-26 updated assembly guide
    [Circuitboard_Mount (Template).FCStd]
2020-08-26 added distinction between long and normal ball bearing and servo mount to 3d printed partlist
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2020-09-18 Added mountingplates and -brackets for the electronics, updated covers and partslist
    [Bottom_Cover (Template).FCStd, Bottom_Cover (Template).stl, Bottom_Cover_Split_Front.FCStd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]
2020-09-20 fixed ESP32-placement in circuitry mountingplate
    [Circuitry_Mountingplate.FCStd, Circuitry_Mountingplate.stl, Circuitry_Mountingplate_Extended.FCStd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]
2020-09-21 added EXPERIMENTAL circuitry mountingplate for raspberry zero
    [EXPERIMENTAL_Circuitry_Mountingplate_Extended_Raspberry_Pi_Zero_W.FCStd, EXPERIMENTAL_Circuitry_Mountingplate_Extended_Raspberry_Pi_Zero_W.stl, EXPERIMENTAL_Ci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]
2020-09-21 updated EXPERIMENTAL circuitry mountingplate for raspberry zero
    [EXPERIMENTAL_Circuitry_Mountingplate_Extended_Raspberry_Pi_Zero_W.FCStd, EXPERIMENTAL_Circuitry_Mountingplate_Extended_Raspberry_Pi_Zero_W.stl, EXPERIMENTAL_Ci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]
2020-09-28 changed default display and added new rear-cover it
    [Rear_Cover_1_77_tft_without_SD.FCStd, Rear_Cover_1_77_tft_without_SD.stl, Rear_Cover_long_1_77_tft_without_SD.FCStd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]
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2020-09-28 update BOM and fix typos
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2020-10-09 Add ESP32-CAM sensor- and cameramount parts. Update assembly guide and partslist
    [cameramount_esp32_cam.FCStd, cameramount_esp32_cam.stl, cameramount_esp32_cam_counterpiece.FCStd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]
2020-10-12 improved Rear Cover with slot for SD card
    [Rear_Cover_long_1_8_tft_with_SD.FCStd, Rear_Cover_long_1_8_tft_with_SD.stl]
2020-10-19 front cover improvement for assemnbly by preventing nuts from slipping out
    [Front_Cover_Optimized.FCStd, Front_Cover_Optimized.stl]
2020-10-30 revised curcuitry mountingplate capable of mounting esp32 devkit v1 and v4
    [Circuitry_Mountingplate.FCStd, Circuitry_Mountingplate.stl, Circuitry_Mountingplate_Extended.FCStd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]
2020-11-09 update BOM and electronics-section
    [SpotMicroESP32_Pinout_v1_0_0.xlsx, SpotMicroESP32_Pinout_v1_0_0_with_ESP32_CAM.xlsx]
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2020-11-19 added images to electronics, updated BOM and descriptions
2020-12-02 add FreeCAD files for electronics modules and add modular rear cover and top cover with OLED
    [0_96_inch_I2C_OLED.FCStd, 1_8_inch_tft_screen.FCStd, 1_8_inch_tft_screen_with_sd_card.FCStd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]
2020-12-02 add screwholes for neopixel ring to top cover
    [Top_Cover_Split_Front.FCStd, Top_Cover_Split_Front.stl]
2020-12-06 update shoulder blocks
    [Bottom_Shoulder.FCStd, Bottom_Shoulder.stl, Top_Shoulder.FCStd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]
2020-12-06 update cameramount and sensormount for ESP32-CAM to fit both the OV2640 Ver.2 & Ver.1
    [cameramount_esp32_cam.FCStd, cameramount_esp32_cam.stl, sensormount_esp32_cam.FCStd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]
2020-12-06 add voltage and current sensor modules to BOM
2020-12-09 add fritzing sketch and update shoulderjoint servomount
    [2020-12-09_Circuitry_final.fzz, Shoulder_Joint_Servomount.FCStd, Shoulder_Joint_Servomount.stl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]
2020-12-17 added circuit mountingplate for SZBK07 configuration. updated some readme's
    [Circuitry_Mountingplate_SZBK07.FCStd, Circuitry_Mountingplate_SZBK07.stl, Circuitry_Mountingplate_SZBK07_Extended.FCStd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]
2021-01-04 added ESP32-CAM interrupt pin to pin-layout
    [SpotMicroESP32_Pinout_v1_1_0_with_ESP32_CAM.xlsx]
2021-01-06 fixed wrong M3 holesize in ESP-CAM Cameramount part
    [cameramount_esp32_cam.FCStd]
2021-01-09 added servohorn 6 b-star model to parts
    [Servohorn_6_B_Star.FCStd, Servohorn_6_B_Star.stl]
2021-01-21 added user generated modifications to parts folder - silicone feet, metaldisc servohorns, rpi zero circuitry mountingplate
    [EXPERIMENTAL_Circuitry_Mountingplate_Extended_Raspberry_Pi_Zero_W.FCStd, EXPERIMENTAL_Circuitry_Mountingplate_Extended_Raspberry_Pi_Zero_W.stl, EXPERIMENTAL_Ci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]
2021-02-03 updated fritzing schematic to account for changes esp-cam connections
    [2020-02-03_Circuitry_final.fzz, 2020-12-09_Circuitry_final.fzz, SpotMicroESP32_Pinout_v1_0_0_with_ESP32_CAM.xlsx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]
2021-03-06 fixed wrong dimensions of Circuitboard Mount Template
    [Circuitboard_Mount (Template).FCStd, Circuitboard_Mount (Template).stl]
2021-03-15 Changed names in Assembly ReadMe + added links
    Changed the names so that they match the parts list, also added links to said section of the part list!
2021-03-15 Added anchor tags for assembly instructions
    Added corresponding anchor tags for assembly instructions for a better "UX"
2021-03-15 Changed all instances of lower leg
    Replaced all instances of lower leg with wrists for better following and concordance!
2021-03-17 added adapter plate modification for neopixel-rings with wider inner diameter
    [Circuitboard_Mount (Template).stl, LED_RING_ADAPTER_PROTOTYPE.FCStd, Led_Ring_Adatper_Prototype.stl]
2021-03-20 Added a variant of the circuitry mounting plate for Arduino
    A variant of the circuitry mounting plate for a simplified version of the circuit for beginners (no LiPo, just C or D batteries) and no cameras or displays
    [Circuitry_Mountingplate_Arduino.FCStd]
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2021-04-26 Modified a few pieces!
    Added a mounting plate for the Arduino & PCA9685 driver (no holes for mounting a LiPo);
    Modifed the servohorn holes as they were too small to comfortably fit M2 screws!
    [Circuitry_Mountingplate_Arduino.FCStd, Circuitry_Mountingplate_Arduino.stl, Servohorn_6_B_Star.FCStd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]
2021-04-26 Update README.md
    Finished (I think) adding links and changing names (in the assembly instructions) to the appropriate places and corresponding names in the parts list!
2021-04-27 fix m2 screwhole sizes in servohorn
    [Servohorn_6_B_Star.FCStd, Servohorn_6_B_Star.stl]
